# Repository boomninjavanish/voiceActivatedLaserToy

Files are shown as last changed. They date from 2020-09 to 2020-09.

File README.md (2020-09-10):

# voiceActivatedLaserToy
## A laser toy that may be activated remotely or at home using Google Assistant and/or Adafruit I/O.
The laser toy stands like a sentry waiting for any cat to approach.

One summer, I decided to vacation in Chile two weeks. After booking a sitter to check on and feed my cat, I realized that I would want to check in on the cat remotely. I setup an Android phone to automatically answer a Skype call so that I may see if the cat is doing well. However, I knew that he would not come to the phone easily. Therefore, with a week before the trip, I designed this toy so that I could play with him remotely while checking in on him. The toy was so successful that I continue to use it to play with the cat to this day!

## Features
* Creates a random play session based on a set of predefined moves. This is to keep the laser game from becoming too predictable.
* Can be activated remotely or on site thanks to Adafruit I/O.
* IFTTT may be used to link with Google Assistant/Home or other services.
* Preoccupied cat...need I say more?

The laser cat toy in action.

## Required Hardware
The following is a bill of materials needed to complete the project:

QTY | Item | Purchase Link
--- | ---- | --------------
1 | Laser Diode - 5mW 650nm Red | [Link](https://www.adafruit.com/product/1054)
1 | Mini Pan-Tilt Kit - Assembled with Micro Servos | [Link](https://www.adafruit.com/product/1967)
1 | Adafruit Feather HUZZAH with ESP8266 | [Link](https://www.adafruit.com/product/2821)
1 | USB A to Micro-B Cable | [Link](https://www.adafruit.com/product/592)
40 | Grams of 3D Printer Filament | [Link](https://shop.prusa3d.com/en/42-prusament)
2 | M2.26 / 4mm Self-Tapping Screws | [Link](https://www.mcmaster.com/99397A322)
4 | M2.5 / 6mm Screws | [Link](https://www.mcmaster.com/94500A213)
4 | M2.5 Hex Nuts | [Link](https://www.mcmaster.com/90592A006)
1 | M3 / 3mm Set Screw | [Link](https://www.mcmaster.com/92605A097)
2-4 | 3M Command Strips with Velcro Backing | [Link](https://www.amazon.com/command-velcro-strips/s?k=command+velcro+strips)
1 | Bored Cat | [Link](https://www.aspca.org/nyc/aspca-adoption-center/adoptable-cats)

## Software

### Adafruit I/O Setup
In order for this project to work, a [Adafruit I/O account](https://io.adafruit.com) is required. The free account has limitations but should be enough for this project to work.

After creating an account, create the following feeds. Note that the feed names must match and are case-sensitive!

* catLaserInitPlay
* catLaserPitch
* catLaserPoll
* catLaserToggle
* catLaserYaw

Next, create a dashboard with the following blocks. All settings are case-sensitive and do not type the quotation marks.

Type | Feed | Settings
---- | ---- | ---------
Toggle | catLaserInitPlay | Button On Text: "PLAYING"; Button Off Text: "OFF"
Slider | catLaserPitch | Slider Min Value: "0"; Slider Max Value: "180"; Slider Step Size: "1"; Slider Label: "Pitch"
Slider | catLaserYaw | Slider Min Value: "0"; Slider Max Value: "180"; Slider Step Size: "1"; Slider Label: "Yaw"
Toggle | catLaserToggle | Button On Text: "ON"; Button Off Text: "OFF"
Line Chart | catLaserPoll | Show History: "24 Hours"; X-Axis Label: "Time"; Y-Axis Label: "Poll Received"; Y-Axis Minimum: "0"; Y-Axis Maximum: "1"; Stepped Line: Checked

### Compilation
This project may be compiled using the [Arduino IDE](https://www.arduino.cc/en/Main/Software). Simply open the project in Arduino, add your WiFi and Adafruit I/O account information to the project according to the instructions contained within sample_config.h. Be sure to change the file name from "sample_config.h" to "config.h" before compiling.

These libraries will be needed in order to compile the software:
* [ESP8266 Board Library and Drivers](https://learn.adafruit.com/adafruit-feather-huzzah-esp8266/using-arduino-ide)
* [ServoEasing](https://github.com/ArminJo/ServoEasing) Learn how to install libraries found [here](https://www.arduino.cc/en/Guide/Libraries).

Be sure to follow the Arduino setup instructions for the Huzzah Feather that are found [here](https://learn.adafruit.com/adafruit-feather-huzzah-esp8266/using-arduino-ide#setup-esp8266-support-2720750-18). 

## Wiring and Assembly

0. Using the USB cable, compile and upload the Arduino sketch included in the source code (see above).
1. Once the case parts have been printed, feed the laser diode into the laser mount then secure it by tightening the M3 set screw in the hole on the side of the barrel.
2. Feed the laser diode wires through the guides on the laser mount then snap the mount into the top of the Mini Pan-Tilt Kit.
3. Measure the amount of wire from the servos and laser diode needed to travel to the bottom case and be soldered to board. Cut the connectors off of the servos and trim the laser diode cable accordingly. 
4. Then feed the wires from both servos and the laser diode in the round hole in the case bottom. Feel free to add heat shrink between the case bottom and the Mini Pan-Tilt Kit for a cleaner look.
5. Solder the wires to the Feather board according to the following schematic:
Schematic for the laser cat toy.
6. Test the connections on the Feather board: plugin the USB to power and attempt to control various functions using the Adafruit I/O dashboard that was created above.
7. Screw the board into the bottom case using the two M2.26 self-tapping screws.
8. Place the four hex nuts on the underside of the case top. The nuts may be glued into place using super glue if desired.
9. Feed the four M2.5 screws through the Mini Pan-Tilt Kit and fasten into the case top.
10. Snap the case top and bottom together.
11. Apply 3M command strips to bottom of case and surface in which the unit will reside.

## Usage
Once the software and hardware has been setup (see above), the laser and movement may be controlled directly via the Adafruit I/O dashboard. A randomized play session may be initiated by toggling the catLaserInitPlay feed to "PLAYING" within the dashboard. If the dashboard is working correctly, IFFT may be setup to link the Adafruit I/O feeds to almost any other service. I have been using Google Assistant to recognize a custom phrase then post "PLAYING" to the catLaserInitPlay feed. [Adafruit has a nice guide on how to setup I/O on IFTTT.](https://learn.adafruit.com/using-ifttt-with-adafruit-io/ifttt-to-adafruit-io-setup) Also, [here is some information on IFTTT.](https://help.ifttt.com/hc/en-us/articles/115010158167-How-does-IFTTT-work-)

## Contributing
If you wish to contribute to this project, feel free to [reach out to me](https://dunlap.media/contact).

## License
This project is protected by the GNU General Public License v3.0. [More information.](https://github.com/boomninjavanish/voiceActivatedLaserToy/blob/master/LICENSE)

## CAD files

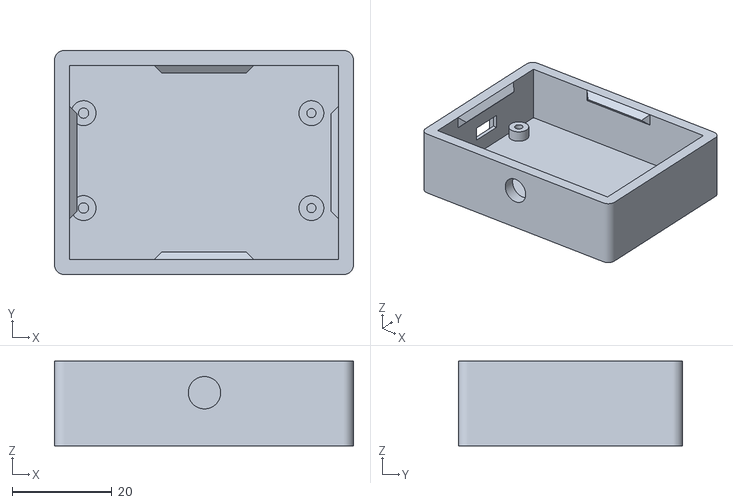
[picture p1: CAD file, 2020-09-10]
case3DPrintFiles/caseBottom.stl
60.0 x 45.0 x 17.0

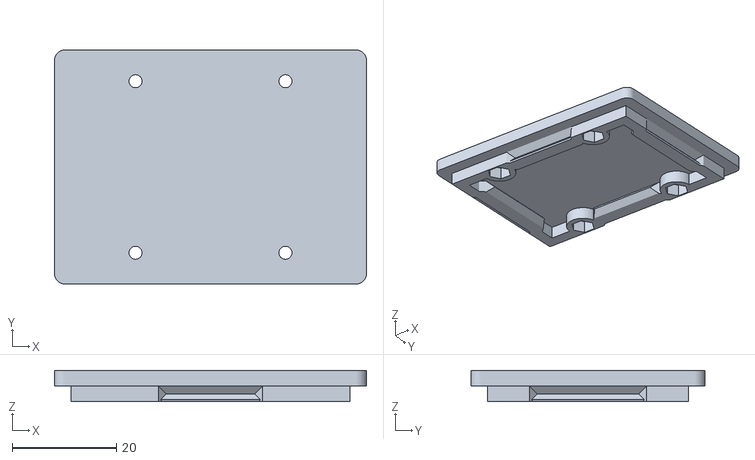
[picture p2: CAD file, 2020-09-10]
case3DPrintFiles/caseTop.stl
60.0 x 45.0 x 6.00

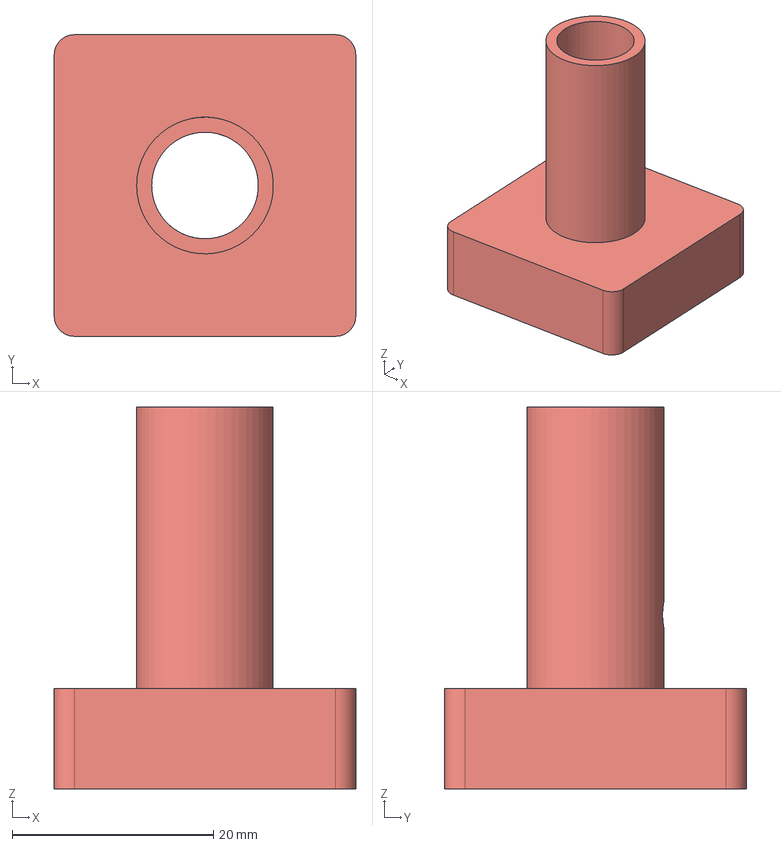
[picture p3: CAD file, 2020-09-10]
case3DPrintFiles/laserMount.step
30.0 x 30.0 x 38.0 mm

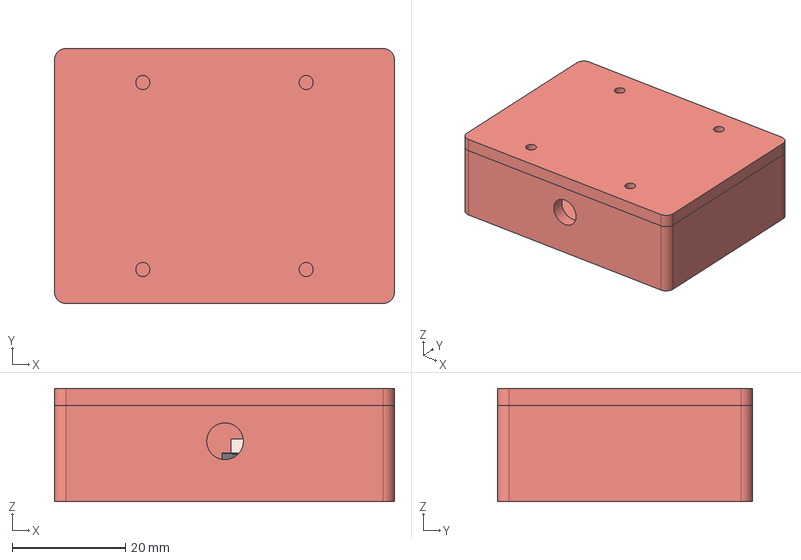
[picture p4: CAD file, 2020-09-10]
case3DPrintFiles/case.step
60.0 x 45.0 x 20.0 mm
ESP8266 v7
ESP8266 v7 (1)
ESP8266 v7 (2)
ESP8266 v7 (3)
ESP8266 v7 (4)
ESP8266 v7 (5)
ESP8266 v7 (6)
ESP8266 v7 (7)
ESP8266 v7 (8)
ESP8266 v7 (9)
ESP8266 v7 (10)
ESP8266 v7 (11)
ESP8266 v7 (12)
ESP8266 v7 (13)
ESP8266 v7 (14)
ESP8266 v7 (15)
ESP8266 v7 (16)
ESP8266 v7 (17)
ESP8266 v7 (18)
ESP8266 v7 (19)
ESP8266 v7 (20)
ESP8266 v7 (21)
ESP8266 v7 (22)
ESP8266 v7 (23)
ESP8266 v7 (24)
ESP8266 v7 (25)
ESP8266 v7 (26)
ESP8266 v7 (27)
ESP8266 v7 (28)
ESP8266 v7 (29)
ESP8266 v7 (30)
ESP8266 v7 (31)
ESP8266 v7 (32)
ESP8266 v7 (33)
ESP8266 v7 (34)
ESP8266 v7 (35)
ESP8266 v7 (36)
ESP8266 v7 (37)
PCB
Battey-con
case

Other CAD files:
case3DPrintFiles/laserMount.stl

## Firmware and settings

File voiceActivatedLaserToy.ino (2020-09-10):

#include <ServoEasing.h>
#include "config.h"
#include "dataStructures.h"

// create the two servos; pitch is the top servo, yaw is the bottom
ServoEasing pitchServo;
ServoEasing yawServo;

// track the state of the yaw and pitch
int currentPitch = 90;
int currentYaw = 90;


// the minimum/maxiumum pitch and yaw; calibrate these to the size of the room
int minPitch = 115;
int maxPitch = 140;

int minYaw = 67;
int maxYaw = 100;

// track the time for heart beat
int currentTime = millis();

// create the feeds from the Adafruit IO
AdafruitIO_Feed *catLaserYawFeed = io.feed("catLaserYaw");
AdafruitIO_Feed *catLaserPitchFeed = io.feed("catLaserPitch");
AdafruitIO_Feed *catLaserInitPlayFeed = io.feed("catLaserInitPlay");
AdafruitIO_Feed *catLaserPollFeed = io.feed("catLaserPoll");
AdafruitIO_Feed *catLaserToggleFeed = io.feed("catLaserToggle");

void setup()
{
    // home servos and setup laser 
    homeLaser();
    pinMode(14, OUTPUT); // laser pin = 14

    // setup serial connection
    Serial.begin(115200);
    // wait for serial monitor
    //while( ! Serial);

    // connect to Adafruit IO Service
    Serial.print("Connecting to Adafruit IO");
    io.connect();

    // handle messages from the Adafruit IO feeds
    catLaserPitchFeed->onMessage(handlePitchMessage);
    catLaserYawFeed->onMessage(handleYawMessage);
    catLaserToggleFeed->onMessage(handleLaserMessage);
    catLaserInitPlayFeed->onMessage(handlePlayMessage);

    // wait for Adafruit IO connection
    while(io.status() < AIO_CONNECTED) 
    {
        // print dots to terminal and blink laser
        Serial.print(".");
        delay(250);
        toggleLaser(HIGH);
        delay(250);
        toggleLaser(LOW);
    }

    // once connected to Adafruit IO
    Serial.println();
    Serial.println(io.statusText());
    catLaserPitchFeed->get();
    catLaserYawFeed->get();
    catLaserToggleFeed->get();

    // reset all status indicators on Adafruit IO
    catLaserToggleFeed->save("OFF");
    catLaserPitchFeed->save(currentPitch);
    catLaserYawFeed->save(currentYaw);

}

void loop()
{
	// stay connected to Adafruit IO and process incoming commands
    io.run();

    // let Adafruit know we are alive
    sendHeartBeatToAdafruit();
}

// turn the servos on or off; send a LOW for off or HIGH for on
void toggleServos(int servosState)
{
    if (servosState == HIGH)
    {
        pitchServo.attach(13); // top servo pin = 13
        yawServo.attach(12); // bottom servo pin = 12
    } else if (servosState == LOW)
    {
        pitchServo.detach();
        yawServo.detach();
    }
}

// turn the laser on and off; send a LOW for off or HIGH for on
void toggleLaser(int laserState)
{
    digitalWrite(14, laserState); // laser pin = 14

    // update Adafruit IO
    String stateName;
    if (laserState == HIGH)
    {
        //catLaserToggleFeed->save("ON");
    } 
    else
    {
        //catLaserToggleFeed->save("OFF");
    }
    
}

// move to laser to home position
void homeLaser(){
    currentPitch = 20;
    currentYaw = 110;
    setSpeedForAllServos(30);
    toggleServos(HIGH);
    pitchServo.setEaseTo(currentPitch);
    yawServo.setEaseTo(currentYaw);
    synchronizeAllServosStartAndWaitForAllServosToStop();

    // make it "pop" back into place
    yawServo.write(90);

    // update the Adafruit IO values
    //catLaserPitchFeed->save(currentPitch);
    //catLaserYawFeed->save(currentYaw);

    delay(2000); // give enough time to get there
    toggleServos(LOW);
}

// handle the Adafruit IO messages for the pitch servo
void handlePitchMessage(AdafruitIO_Data *data)
{
    int angle = data->toInt();
    toggleServos(HIGH);
    pitchServo.write(angle);
    delay(2000);
    toggleServos(LOW);
}

// handle the Adafruit IO messages for the pitch servo
void handleYawMessage(AdafruitIO_Data *data)
{
    int angle = data->toInt();
    toggleServos(HIGH);
    yawServo.write(angle);
    delay(2000);
    toggleServos(LOW);
}

// handle the Adafruit IO messages for turning the laser on and off
void handleLaserMessage(AdafruitIO_Data *data)
{
    String state = data->toString();
    if (state == "ON")
    {
        toggleLaser(HIGH);
    } else if (state == "OFF")
    {
        toggleLaser(LOW);
    }
}

// handle the Adafruit IO messages for initiation of play session
void handlePlayMessage(AdafruitIO_Data *data)
{
    String toggleValue = data->toString();
    
    if(toggleValue == "PLAYING")
    {
        // start play session
        makeRandomCommandSet();
        executePlayCommandSet(randomCommandSet, 50);
        //executePlayCommandSet(laserWallJump, countElements(laserWallJump));
        makeRandomCommandSet();
        executePlayCommandSet(randomCommandSet, 50);

        catLaserInitPlayFeed->save("OFF");
        homeLaser();
    
    } 
}

// sends a '1' to Adafruit IO every minute to let it know we are alive
void sendHeartBeatToAdafruit()
{
    int timeDifferential = millis() - currentTime;
    if (timeDifferential > 60000)
    {
        catLaserPollFeed->save(1);
        currentTime = millis();
    }
}

// execute a play command setup
void executePlayCommandSet(PlayCommandSet commandSet[], int elementsInCommandSet)
{
    // attach servos
    toggleServos(HIGH);

    setSpeedForAllServos(140);

    for (int i = 0; i < elementsInCommandSet; i++)
    {
        
        toggleLaser(commandSet[i].laserToggle);

        // smoothly move laser to next location
        int diffBetweenPitch = commandSet[i].pitch - commandSet[i-1].pitch;

        pitchServo.setEaseTo(commandSet[i].pitch);
        yawServo.setEaseTo(commandSet[i].yaw);
        synchronizeAllServosStartAndWaitForAllServosToStop();

        delay(commandSet[i].delayTime);
    }

    // detach servos and shutoff laser
    toggleServos(LOW);
    toggleLaser(LOW);
}

// make a laser floor trace game
 void makeRandomCommandSet()
{
    //int numberOfElements = countElements(randomCommandSet);
    int numberOfElements = 50;

    for (int i = 0; i < numberOfElements; i++)
    {
        // consitent delay between movements
        randomCommandSet[i].delayTime = random(300,500);

        // rarely turn off the laser
        int randomNumber = random(50);
        if (randomNumber == random(50))
        {
            randomCommandSet[i].laserToggle = LOW;
        }
        else
        {
            randomCommandSet[i].laserToggle = HIGH;
        }

        // keep pitch between 120 and 180
        randomCommandSet[i].pitch = random(minPitch, maxPitch);

        // keep yaw between 30 and 100
        randomCommandSet[i].yaw = random(minYaw, maxYaw);
    }
}

// count the number of elements in the command set
int countElements(PlayCommandSet commandSet[])
{        
    int elementsInCommandSet = sizeof(commandSet) / sizeof(commandSet[0]);
    return elementsInCommandSet;
}
